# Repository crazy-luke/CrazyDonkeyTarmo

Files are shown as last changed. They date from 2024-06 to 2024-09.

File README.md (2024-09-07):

## [English README](./README_EN.md) 👈
----

# CrazyDonkeyTarmo

`CrazyDonkeyTarmo` 项目目标是保留高性能RC车乐趣的同时能开展学习自动驾驶技术。  
项目深度改造 Tarmo5 RC 车， 结合 DonkeyCar 自动驾驶项目。

## 视频介绍
* 《造车篇》： https://www.bilibili.com/video/BV1qM4m1U7vm
* 《自动驾驶篇》: https://www.bilibili.com/video/BV12aHZeXEUs

---
## 车辆制作 (Hardwear_Car)
* [CDT_Assemble.pdf](./Hardwear_Car/CDT_Assemble.pdf) ： 组装说明书
* STL： 3D 打印文件 （打印参数见 `stl/README.md` )
* [Parts.md](./Hardwear_Car/Parts.md): 视频中使用的部分零件

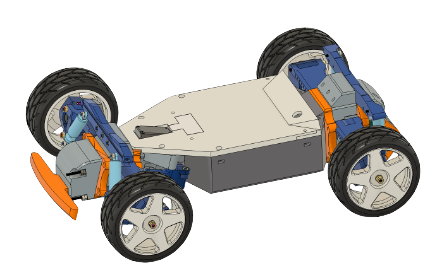
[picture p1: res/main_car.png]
main_car
 

## PCB电路 （Optinal)
* PCB_CrazyDonkeyTarmoBoard：超级电源板 
* PCB_CrazyPowerBoard： 探路者控制板 
    * BOM.csv: 采购元件清单
    * ibom.html：元件摆放(细节见PNG图片)
    * Gerber：PCB生产
    * Schematic：原理图
* 电路连接: [Wiring Diagram.jpg](./Hardwear_Car/wiring_diagram.jpg)

---
## 自动驾驶篇 (Softwear_SelfDrive)
* [星辰探路者自动驾驶系统手册](./Softwear_SelfDrive/README.md)
* [扩展篇-物件识别](./Softwear_SelfDrive/crazydonekytarmo_od.md) （Optinal)
* myconfig: 探路者配置参考文件

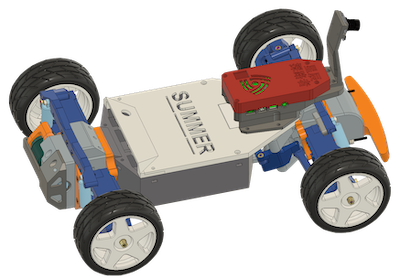
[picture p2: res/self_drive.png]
self_drive


## Reference
* [tarmo5](https://www.reddit.com/r/EngineeringNS/comments/zvellk/tarmo5/)
* [donkeycar](https://www.donkeycar.com/)

## License

<br />This work is licensed under a <a rel="license" href="http://creativecommons.org/licenses/by-nc-nd/4.0/">Creative Commons Attribution-NonCommercial-NoDerivatives 4.0 International License</a>.

Copyright © 2024, 疯狂豆®

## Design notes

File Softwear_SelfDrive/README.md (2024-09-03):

# 星辰探路者自动驾驶系统手册

本文描述基于 **Donkeycar** 搭建 **星辰探路者** 自动驾驶搭建全过程

## Hardware 
  * CrazyDonkeyTarmo 车
  * 树莓派
    * [Raspberry Pi](https://docs.donkeycar.com/guide/robot_sbc/setup_raspberry_pi/): 4B 4GB
    * [Camera](https://docs.donkeycar.com/parts/cameras/): 160 degree wide angle
    * microSD: 128G A2 U3 
      
------
##  一、安装系统
### Raspberry Pi

DonkeycarDoc:[Get Your Raspberry Pi Working](https://docs.donkeycar.com/guide/robot_sbc/setup_raspberry_pi/)

1. **安装树莓派 OS**
  * 操作： SD卡插入电脑
  * 安装工具: [Raspberry Pi Imager](https://www.raspberrypi.com/software/)
    * Choose
      * Choose divice: `raspberry pi 4`
      * Choose OS: `Raspberry Pi OS Lite 64-bit Bookworm`
      * Choose Storage: `SD`
    * Edit Settings
      * hostname: `crazydonkeytarmo-1`
      * username: `luke`, password: `123456`
      * SSID,  Password, Country
      * Enable SSH
  * 操作：SD插入树莓派，树莓派和电脑处于同一个网络，通电

  * 修改莓派修改配置
    
      ```
      # 电脑通过 SSH 连接树莓派
      # ssh username@ip
      # ssh username@hostname.local

      ssh luke@crazydonkeytarmo-1.local 

      # 进入配置
      sudo raspi-config
      ```
      配置界面依次选择：Advanced Options -> Expand Filesystem -> Finish -> reboot

2. **升级环境**

  * 升级软件包
    ```
    # Update and Upgrade
    sudo apt-get update --allow-releaseinfo-change
    sudo apt-get upgrade
    ```

  * 设置 Python 虚拟环境
    ```
    #创建一个名为env的虚拟环境，命令执行完毕后会出现一个env文件夹
    python3 -m venv env --system-site-packages

    #每次开机都会自动进入env的虚拟环境
    echo "source ~/env/bin/activate" >> ~/.bashrc
    source ~/.bashrc
    ```

  * 提前安装后续可能遇到错误的库（optinal)
    ```
    # libcap：捕获 过滤 分析 存储网络数据包
    sudo apt install libcap-dev

    # psutil：获取系统的信息， h5py：读写HDF5文件格式
    sudo apt-get install gcc python3-dev
    pip install psutil
    pip install h5py --only-binary h5py

    # python3-libcamera: 摄像头
    sudo apt install -y python3-libcamera
    
    # python3-kms++
    sudo apt install -y python3-kms++
    ```

3. **Donkeycar Code**

  * 下载源码
    ```
    # 安装git库
    sudo apt install git

    # 下载Git代码
    cd ~
    git clone https://github.com/autorope/donkeycar.git
    cd donkeycar
    
    # 切换版本
    git checkout 5.1.0

    # 编译安装 
    pip install -e .[pi]
    # zsh shell
    pip install -e .\[pi\]
    ```

  * 验证 tensorflow (optinal)
  ```
  python -c "import tensorflow; print(tensorflow.__version__)"
  ```

### 创建 CrazyDonkeyTarmo

1. [Create your car application 创建应用](https://docs.donkeycar.com/guide/create_application/)

    ```
    donkey createcar --path ~/crazydonkeytarmo

    cd ~/crazydonkeytarmo
    ```

2. 配置 [控制器](https://docs.donkeycar.com/parts/rc/)

  * 启用 pigpiod
    ```
    sudo systemctl enable pigpiod & sudo systemctl start pigpiod
    ```

  * 编辑 ~/crazydonkeytarmo/myconfig.py

    1. 从树莓派下载 myconfig.py 文件到电脑
    ```
    #电脑开一个新的终端
    #scp <username>@<ip>:<src_file> <des_file>

    scp luke@crazydonkeytarmo-1.local:/home/luke/crazydonkeytarmo/myconfig.py .
    ```

    2. 电脑打开 myconfig.py 文件并修改下面字段

    * 开启 pigpio
      ``` 
      CONTROLLER_TYPE = 'pigpio_rc'
      USE_JOYSTICK_AS_DEFAULT = True
      DRIVE_TRAIN_TYPE = "PWM_STEERING_THROTTLE"
      ```
    * 修改 PWM 输入信号（RC接收机 -> 树莓派）
      ```
      #PIGPIO RC control
      STEERING_RC_GPIO = 3              # CrazyDonkeyTarmoBus - s_in
      THROTTLE_RC_GPIO = 15             # CrazyDonkeyTarmoBus - t_in
      DATA_WIPER_RC_GPIO = 4            # CrazyDonkeyTarmoBus - ext
      PIGPIO_STEERING_MID = 1500         # Adjust this value if your car cannot run in a straight line
      PIGPIO_MAX_FORWARD = 2000          # Max throttle to go fowrward. The bigger the faster
      PIGPIO_STOPPED_PWM = 1500
      PIGPIO_MAX_REVERSE = 1000          # Max throttle to go reverse. The smaller the faster
      PIGPIO_SHOW_STEERING_VALUE = False
      PIGPIO_INVERT = False
      PIGPIO_JITTER = 0.025   # threshold below which no signal is reported
      ```
    * 打开 PWM 输出配置 （树莓派 -> 方向舵机和动力电机）
      ```
      # 打开PWM_STEERING_THROTTLE字段，修改PIN
      PWM_STEERING_THROTTLE = {
          "PWM_STEERING_PIN": "PIGPIO.BCM.2",   # CrazyDonkeyTarmoBus - s-out
          "PWM_THROTTLE_PIN": "PIGPIO.BCM.14",  # CrazyDonkeyTarmoBus - t-out
          .....
      }
      ```
    
    * 其他配置  Optinal
      ```
      # 修改摄像头
      CAMERA_TYPE = "PICAM"
      IMAGE_W = 320
      IMAGE_H = 240

      # 关闭自动录制
      AUTO_RECORD_ON_THROTTLE = False
      ```

    * 修改后的 myconfig.py 文件上传到树莓派
    ```
    #电脑 -> 树莓派
    #scp <src_file> <username>@<ip>:<des_file>

    scp myconfig.py luke@crazydonkeytarmo-1.local:/home/luke/crazydonkeytarmo/
    ```    

4. 测试
  注意：**关闭ESC电调开关**

  * 启动 crazydonkeytarmo应用
    ```
    #终端连接树莓派
    ssh luke@crazydonkeytarmo-1.local 

    #启动
    cd ~/crazydonkeytarmo
    python manage.py drive
    ```
  * 电脑浏览器访问
    http://ip:8887/drive
   
    如 http://crazydonkeytarmo-1.local:8887/drive

  * 关闭crazydonkeytarmo应用
  终端 `ctrl+c`

### 校准 

1. 官方[驴车参数](https://docs.donkeycar.com/parts/rc_hat/#controlling-esc-and-steering-servo-with-rc-hat)

2. CrazyDonkeyTarmo 参考参数
```
# 注：RC 接收机58hz,官方默认参数60hz, 修改 SCALE 为1.03
PWM_STEERING_THROTTLE = {
    "PWM_STEERING_PIN": "PIGPIO.BCM.2",   # PWM output pin for steering servo
    "PWM_STEERING_SCALE": 1.03,             # used to compensate for PWM frequency differents from 60hz; NOT for adjusting steering range
    "PWM_STEERING_INVERTED": False,         # True if hardware requires an inverted PWM pulse
    "PWM_THROTTLE_PIN": "PIGPIO.BCM.14",   # PWM output pin for ESC
    "PWM_THROTTLE_SCALE": 1.0,              # used to compensate for PWM frequence differences from 60hz; NOT for increasing/limiting speed
    "PWM_THROTTLE_INVERTED": False,         # True if hardware requires an inverted PWM pulse
    "STEERING_LEFT_PWM": 200,               #pwm value for full left steering
    "STEERING_RIGHT_PWM":400,              #pwm value for full right steering
    "THROTTLE_FORWARD_PWM": 400,            #pwm value for max forward throttle
    "THROTTLE_STOPPED_PWM": 300,            #pwm value for no movement
    "THROTTLE_REVERSE_PWM": 200,            #pwm value for max reverse throttle
}
```

------
## 二、自动驾驶

### 收集训练数据
* 树莓派连接手机[网络(Bookworm)](https://www.raspberrypi.com/documentation/computers/configuration.html#configuring-networking)
  ```
  #终端连接树莓派
  ssh luke@crazydonkeytarmo-1.local 

  #查看网络
  sudo nmcli dev wifi list

  #连接网络 (例如 AiPhone)
  sudo nmcli --ask dev wifi connect AiPhone

  #查看网络连接优先级
  nmcli --fields autoconnect-priority,name connection

  #调整优先级（数字越大优先级越高）
  sudo nmcli connection modify AiPhone connection.autoconnect-priority 2
  ```
* 手机安装SSH应用 APP ： `Termius`

2. 采集训练数据

* SSH 连接树莓派
  ```
  ssh luke@crazydonkeytarmo-1.local 
  cd crazydonkeytarmo

  #清理历史数据(optinal)
  #rm -rf ./data/*

  #开始驾驶
  python manage.py drive
  ```
* 开始录制
浏览器访问 http://crazydonkeytarmo-1.local:8887/drive
User-> Start Reconrding
**Let's Go~~~~**

### 训练数据
1. 树莓派训练数据上传到电脑
```
## 树莓派crazydonkeytarmo 目录同步下载到电脑上（初次）
rsync -rv --progress --partial luke@crazydonkeytarmo-1.local:~/crazydonkeytarmo/  ./crazydonkeytarmo

## 树莓派 data目录同步下载到电脑上 crazydonkeytarmo 目录中
# cd crazydonkeytarmo 
# rsync -rv --progress --partial luke@crazydonkeytarmo-1.local:~/crazydonkeytarmo/data/  ./data
```

2. 电脑安装 donkeycar （初次)
```
git clone https://github.com/autorope/donkeycar.git
cd donkeycar
git checkout 5.1.0

#删除已经存在的环境
#conda activate base
#sudo conda env remove -n donkey

conda create -n donkey python=3.11
conda activate donkey
#确认当前已经处于 donkey
conda env list  

#安装
#pip install donkeycar\[pc\]
pip install -e .\[pc\]
```

3. [训练模型](https://docs.donkeycar.com/guide/deep_learning/train_autopilot/)
  
  * 启动donkey ui
    ```
    conda activate donkey
    sudo donkey ui
    ``` 
    * Load car directory:  选择 crazydonkeycar 目录
    * Load tube: 选择 crazydonkeycar 中的data目录（训练数据）
    * Delete: 删除不需要的数据区域(optinal)

  * 通过 [donkey ui](https://docs.donkeycar.com/utility/ui/) 训练
    `Trainer -> Train`
  * 通过命令行训练（optinal, 适合数据量较大)
    ```
    # 用 data 目录下的数据训练一个名为 cdt1 的模型
    donkey train --tub ./data  --model ./models/cdt1
    ```
  * [Train model using GPU for FREE on google golab](https://colab.research.google.com/drive/1CALMB7GioBEUcWNCuHQjrWCT4r01p6Qh)
4. 可能遇到的错误(optinal)
     
     ```
     ## v5.1.0  
     ## ValueError: Key image is not in available keys.
     ## fix: 设置 albumentations==1.4.6
     sudo pip uninstall -y albumentations && pip install albumentations==1.4.6
     ```

### 开始自动驾驶

1. 上传训练完成的 Model 到树莓派
   ```
   #上传模型到树莓派
   #进入电脑的 crazydonkeytarmo 目录执行
   rsync -rv --progress --partial ./models/ luke@crazydonkeytarmo-1.local:~/crazydonkeytarmo/models/
   ```
2. 自动驾驶
    ```
    # 连接 树莓派
    ssh luke@crazydonkeytarmo-1.local 
    cd ~/crazydonkeytarmo

    # 启动模型
    python manage.py drive --model ./models/cdt1.tflite --type tflite_linear
    ```

### 扩展篇
  
 [物件识别](./crazydonekytarmo_od.md)

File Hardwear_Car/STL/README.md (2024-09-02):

# CrazyDonkeyTarmo PRINTED PARTS
---
> Filament:  
> `ABS`: 20% lighter compared to PETG  (ABS 比 PETG重量轻20%)  
> `PETG`: More resistant to UV light compared to ABS  (PETG 比 ABS 更耐紫外线)

## Main Parts
| File | Num | filament  | fill | wall| supports|
| ---|:---:| ---:| ----:|----:|----:|
| TORQUE DAMPER Fit | 2 | TPU95 | 100% | 8 | No
| MOTO MOUNT Fit | 1 | TPU95 | 10% | 6 | No
| FRONT A PLATE FIT | 1 | TPU95 | 10% | 8 | No
| FRONT B PLATE | 1 | TPU95 | 10% | 8 | No
| REAR A PLATE FIT  | 1 | TPU95 | 10% | 8 | No
| REAR B PLATE | 1 | TPU95 | 10% | 8 | No
| Bumper | 1 | TPU95 | 10% | 4 | No
| CONTROL ARM FIT | 8 | ABS/PETG | 10% |9| YES
| FRONT BEARING HUB A05 Fit | 1 | ABS/PETG | 10% |8| No
| FRONT BEARING HUB A06 Fit | 1 | ABS/PETG | 10% |8| No
| FRONT SUS MOUNT Fit | 2 | ABS/PETG | 10% |8| YES
| FRONT AXLE Fit | 2 | PACF  | 10% |8| No
| MAIN GEAR HUB | 1 | PACF  | 10% |8| No
| REAR BEARING HUB  | 2 | ABS/PETG | 10% |8| No
| SHOCK MOUNT FRONT Fit|1 |PACF/PETG  | 10% | 12 or 8| NO
| SHOCK MOUNT REAR Fit  | 1 | PACF/PETG  | 10% |8| No
| STEERING BAR Fit DS3225  | 1 | ABS/PETG | 10% |8| NO
| STEERING ARM A07 FIT  | 1 | ABS/PETG  | 10% |8| YES
| STEERING ARM A08 FIT | 1 | ABS/PETG  | 10% |8| YES
| GEARBOX | 1| ABS/PETG | 10% |3| No
| END CHASSIS B05 | 1| ABS/PETG | 10% |3| No
| END CHASSIS B06 | 1| ABS/PETG | 10% |3| No
| END CHASSIS B04 Fit| 1| ABS/PETG | 10% |3| YES
| GEARBOX LID | 1| ABS/PETG | 10% |3| YES
| CHASSIS Ext | 1 | ABS/PETG | 10% |3| YES
| CHASSIS Cover body | 1 | ABS/PETG | 10% |3| NO
| CHASSIS Cover rear | 1 | ABS/PETG | 10% |3| NO
| CHASSIS Cover window  | 1 | ABS/PETG | 10% |3| NO
| MAIN GEAR herringbone  | 1 | PA/ABS  |  10% |8| NO
| PINION GEAR herringbone  | 1 | PA/ABS  |  10% |8| NO
| STEERING Link Fit  | 2 | PA/PACF | 20% |8| NO
| CV CAGE Fit | 4 | PACF | 10% |8| NO
| CV INNER RACE | 4 | PACF | 10% |8| No
| CV WHEEL HOUSING Fit  | 2 | PACF | 10% |8| No
| FRONT WHEEL SPACER Fit | 4 | PACF | 10% |8| No
| CV GEAR HOUSING Fit  | 2 | PACF | 10% |8| No

## Extension
| File | Num | filament  | fill | wall| supports|
| ---|:---:| ---:| ----:|----:|----:|
| SHOCK MOUNT FRONT LIGHT|1 |PACF/PETG/ABS| 10% | 12 or 8| NO
| LIGHT Wire Cover H | 1 | - | 10% | 3 | NO
| Cover_rear_Light_L  | 1 | - | 10% | 3 | NO
| Cover_rear_Light_LH  | 1 | - | 10% | 3 | NO
| CrazyPowerBoard_Base  | 1 | - | 10% | 3 | NO

## Self Drive Parts

| File | Num | filament  | fill | wall| supports|
| ---|:---:| ---:| ----:|----:|----:|
| FSD_Cam | 1 | - | 10% | 3 | NO
| FSD_Shell_cover | 1 | - | 10% | 3 | NO
| FSD_Shell_main | 1 | - | 10% | 3 | NO
| FSD_Bottom | 1 | - | 10% | 3 | NO

----
## My Print settings 
* PACF
```
Printing Temperature : 255
Print Speed : 80～100
Build Plate Temperature : 70
Fan Speed : OFF
```

* PA12
```
Printing Temperature : 270
Build Plate Temperature : 80
Print Speed : 100
Fan Speed 20%
```

* TPU95
```
Printing Temperature : 235
Build Plate Temperature : 50
Print Speed : 55
Fan Speed : 100%
```

* PETG
```
Printing Temperature : 240
Build Plate Temperature : 55
Print Speed : 170
Fan Speed : 50%
```

* ABS
```
Printing Temperature : 240
Build Plate Temperature : 95
Print Speed : 160
Fan Speed : 30%
```

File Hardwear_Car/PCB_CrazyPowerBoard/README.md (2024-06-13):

# CrazyDonkeyTarmo

Todo: Currently being organized, please be patient.
项目资料还在更新中，目前已经开放 RC 车制作部分。

CrazyDonkeyTarmo 项目目标是保留高性能RC车乐趣的同时能开展学习自动驾驶技术。
项目深度改造 Tarmo5 RC 车， 结合 DonkeyCar 自动驾驶项目。

----
## 车辆硬件制作
* CDT_Assemble.pdf ： 组装说明 (P1-车辆)
* STL： 3D 打印文件
main_car

## PCB电路 （Optinal)
* PCB_CrazyPowerBoard： 探路者控制板 
* PCB_CrazyDonkeyTarmoBoard：超级电源板 

## 自动驾驶篇 (Todo)
Todo

## Reference
* [tarmo5](https://www.reddit.com/r/EngineeringNS/comments/zvellk/tarmo5/)
* [donkeycar](https://www.donkeycar.com/)

## License

<br />This work is licensed under a <a rel="license" href="http://creativecommons.org/licenses/by-nc-nd/4.0/">Creative Commons Attribution-NonCommercial-NoDerivatives 4.0 International License</a>.

Copyright © 2024, 疯狂豆®

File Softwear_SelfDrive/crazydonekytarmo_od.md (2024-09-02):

# 星辰探路者自动驾驶系统手册（扩展篇）

本文描述基于 **Mediapipe** 识别目标增强探路者自动驾驶能力。
内容包括：  
1. 使用预训练模型 识别 `STOP` 标志，车辆执行动作： **停止 -> 等待 -> 前进**
2. 使用预训练模型 识别特定物件， 车辆执行动作：**绕过障碍物**
3. 使用 MediaPipe Maker 迁移学习训练自定义模型 

## Object Detection 测试

### 电脑上测试
* [MediaPipe studio](https://mediapipe-studio.webapps.google.com/home)
* [Labelmap](https://storage.googleapis.com/mediapipe-tasks/object_detector/labelmap.txt)
* [Models](https://ai.google.dev/edge/mediapipe/solutions/vision/object_detector#configurations_options)

### 树莓派上运行 Demo

1. Google 官方样例

  [MediaPipe for Raspberry Pi](https://github.com/google-ai-edge/mediapipe-samples/tree/main/examples/object_detection/raspberry_pi)

```
# SSH 连接树莓派
ssh luke@crazydonkeytarmo-1.local 

# 下载代码
cd ~
git clone https://github.com/google-ai-edge/mediapipe-samples.git

# 设置环境，下载模型
cd mediapipe-samples/examples/object_detection/raspberry_pi
sh setup.sh

# 安装缺少 OpenCV 依赖的 OpenGL 库 (Optinal)
sudo apt install -y libgl1-mesa-glx

# 运行
python3 detect.py   --model efficientdet.tflite

## 摄像头驱动问题，报错和解决参考
# ERROR: Unable to read from webcam. Please verify your webcam settings.
>> https://github.com/google-ai-edge/mediapipe-samples/issues/383

```

2. 星辰探路者 测试代码
   
```
# 上传 mediapipe_cdt
rsync -rv --progress --partial ./mediapipe_cdt/ luke@crazydonkeytarmo-1.local:~/mediapipe_cdt/

# SSH 连接树莓派
ssh luke@crazydonkeytarmo-1.local 
cd mediapipe_cdt

# 下载模型文件 efficientdet_lite0.tflite
wget -q -O efficientdet_lite0.tflite -q https://storage.googleapis.com/mediapipe-models/object_detector/efficientdet_lite0/int8/1/efficientdet_lite0.tflite

# 运行 
# Headless (Text Only)
python3 detect_cdt_text.py   --model efficientdet_lite0.tflite --maxResults 2 --scoreThreshold 0.51 --frameWidth 320 --frameHeight 240

```
```
#fix issue: module 'cv2' has no attribute 'flip'
pip install opencv-python

Looking in indexes: https://pypi.org/simple, https://www.piwheels.org/simple
Collecting opencv-python
  Using cached opencv_python-4.10.0.84-cp37-abi3-manylinux_2_17_aarch64.manylinux2014_aarch64.whl.metadata (20 kB)
Requirement already satisfied: numpy>=1.21.2 in /home/luke/env/lib/python3.11/site-packages (from opencv-python) (1.26.4)
Using cached opencv_python-4.10.0.84-cp37-abi3-manylinux_2_17_aarch64.manylinux2014_aarch64.whl (41.7 MB)
Installing collected packages: opencv-python
Successfully installed opencv-python-4.10.0.84
```

## 使用预训练模型

👉 [MR to donkeycar](https://github.com/autorope/donkeycar/pull/1197)

工程改动说明
```
- donkeycar/donkeycar/parts/object_detector/
├── mediapipe_object_detetor.py   ## mediapipe object detection
├── detector_manager.py           ## 识别模块总调度
├── action_stop_and_go.py         ## StopAndGo  停止车辆 -> 等待 -> 前进
├── action_pass_object.py         ## PassObject 绕过障碍物

- donkeycar/donkeycar/templates/
├── complete.py         ## 加载 detector_manager 模块
├── cfg_complete.py     ## 增加 object detection 开关配置

- donkeycar/
├── setup.cfg           ## 增加 mediapipe 依赖

```

创建新应用
```
# SSH 连接树莓派
ssh luke@crazydonkeytarmo-1.local 
cd donkeycar

# 安装依赖 
pip install mediapipe

# 编译(optinal)
pip install -e .[pi]
# pip install -e .\[pi\]

# 创建新应用 crazydonkeytarmo_od
donkey createcar --path ~/crazydonkeytarmo_od
cd ~/crazydonkeytarmo_od

# 下载模型文件物件识别模型文件
# https://storage.googleapis.com/mediapipe-models/object_detector/efficientdet_lite0/int8/1/efficientdet_lite0.tflite
# 上传自定义物件识别模型
# scp android_toy_model.tflite luke@crazydonkeytarmo-1.local:/home/luke/crazydonkeytarmo/

# 上传文件到树莓派：修改后的配置, 自动驾驶驾驶模型，物件识别模型
rsync -rv --progress --partial ./crazydonkeytarmo_od/ luke@crazydonkeytarmo-1.local:~/crazydonkeytarmo_od/
```

# 运行自动驾驶

* 测试识别指定标签
* `STOP` 标志动作
* 绕过障碍物

```
cd crazydonkeytarmo_od

# 1. 配置 myconfig.py： OBJECT_DETECTOR 

# 2. 运行
python manage.py drive --model ./models/cdt1.tflite --type tflite_linear

# 3. 浏览器访问 http://crazydonkeytarmo-1.local:8887/drive
```

## Transefer 训练自己的模型

[MediaPipe model maker](https://ai.google.dev/edge/mediapipe/solutions/model_maker)

[Object detection model customization](https://ai.google.dev/edge/mediapipe/solutions/customization/object_detector)

## Ref

* [mediapipe-samples: object detection on raspberry](https://github.com/google-ai-edge/mediapipe-samples/tree/main/examples/object_detection/raspberry_pi)

* [MediaPipe maker exaple: Object_Detection_for_3_dogs](https://colab.research.google.com/github/googlesamples/mediapipe/blob/main/tutorials/object_detection/Object_Detection_for_3_dogs.ipynb)

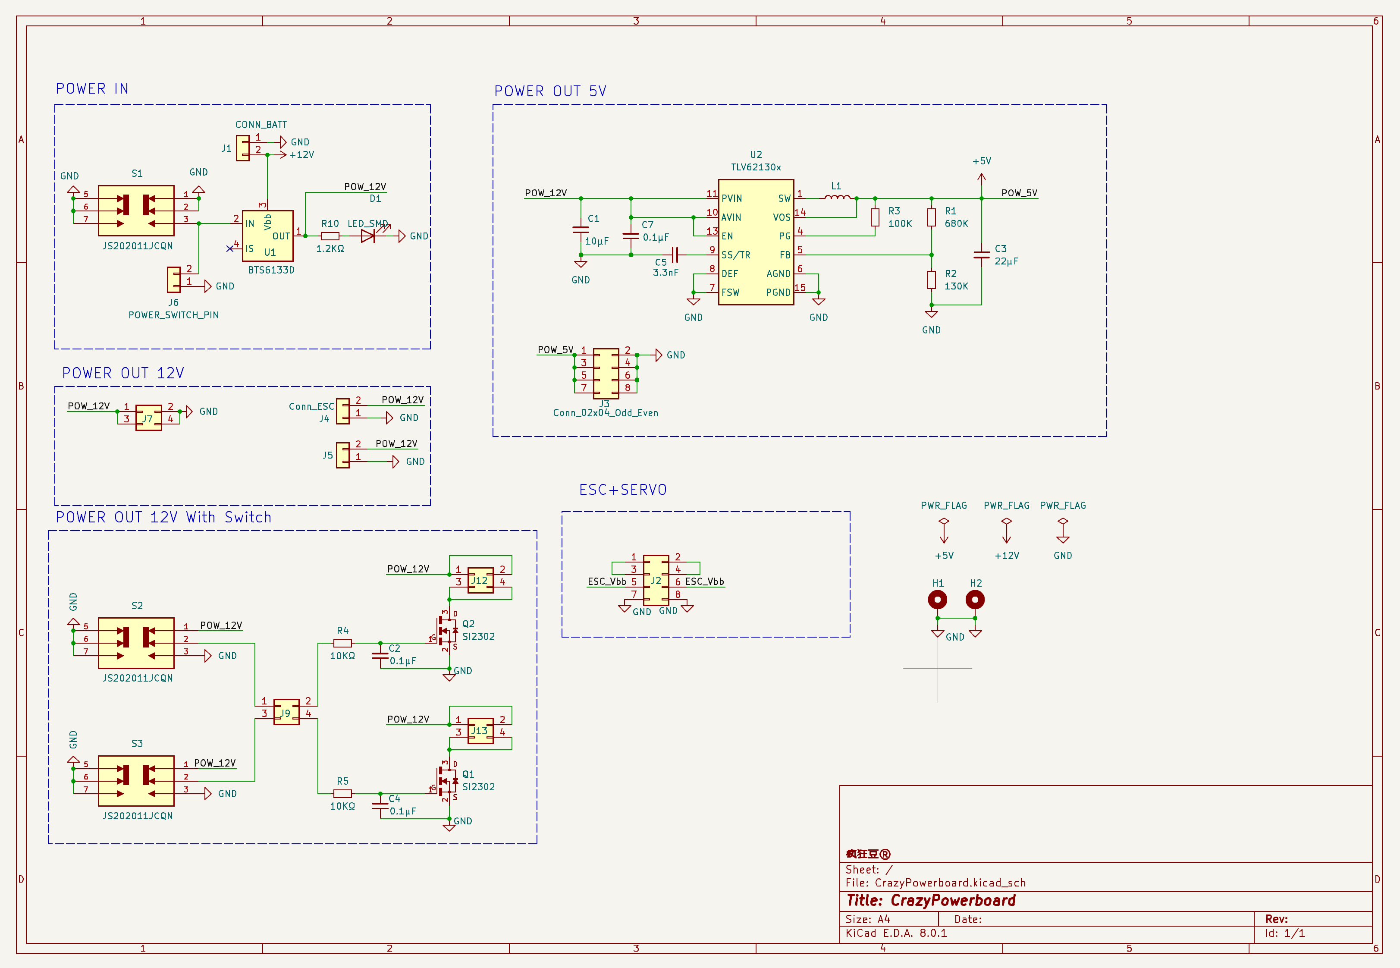
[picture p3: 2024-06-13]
Hardwear_Car/PCB_CrazyPowerBoard/Schematic.png

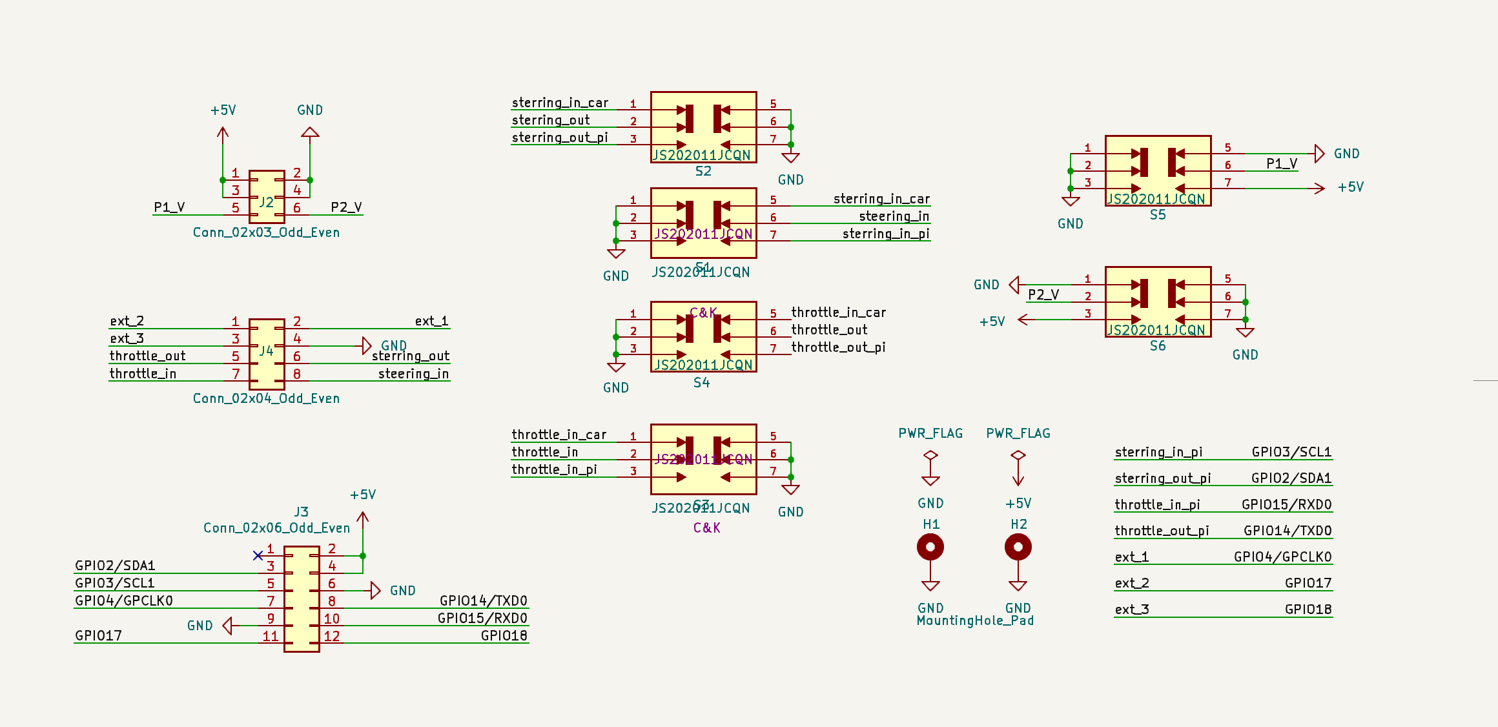
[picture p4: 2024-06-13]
Hardwear_Car/PCB_CrazyDonkeyTarmoBoard/Schematic.png

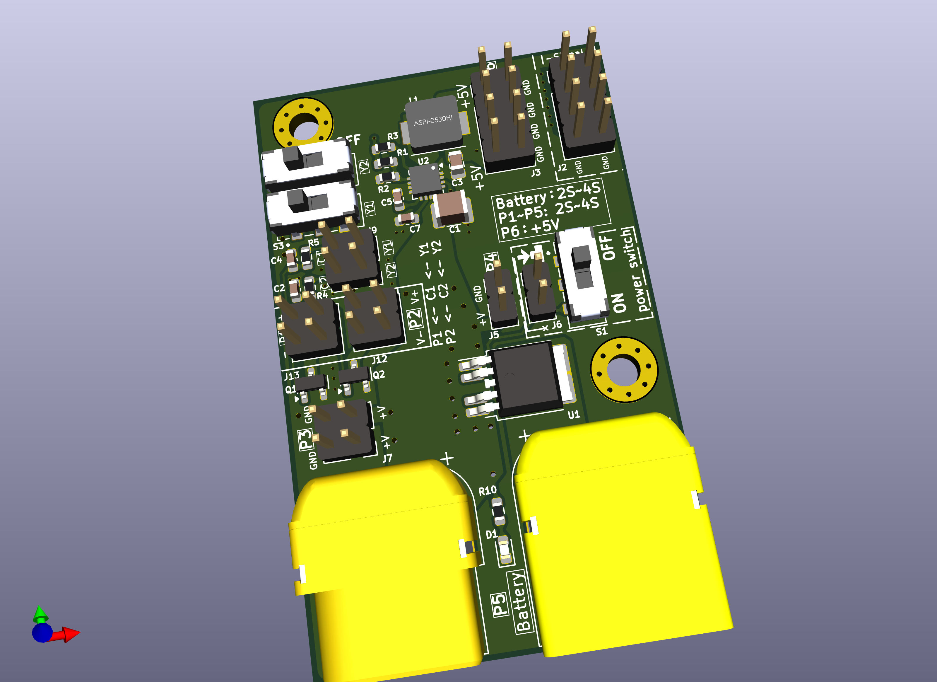
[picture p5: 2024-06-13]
Hardwear_Car/PCB_CrazyPowerBoard/CrazyPowerboard_1.png

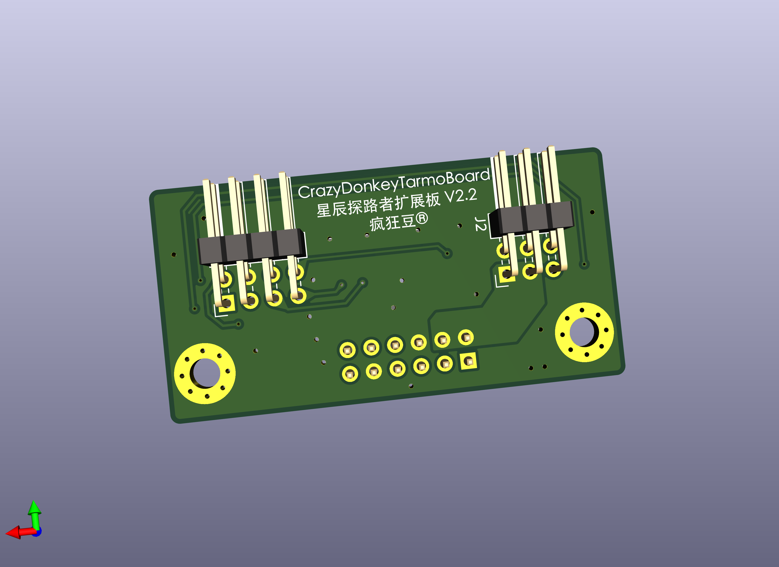
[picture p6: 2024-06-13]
Hardwear_Car/PCB_CrazyDonkeyTarmoBoard/CrazyDonkeyTarmoBoard_2.png

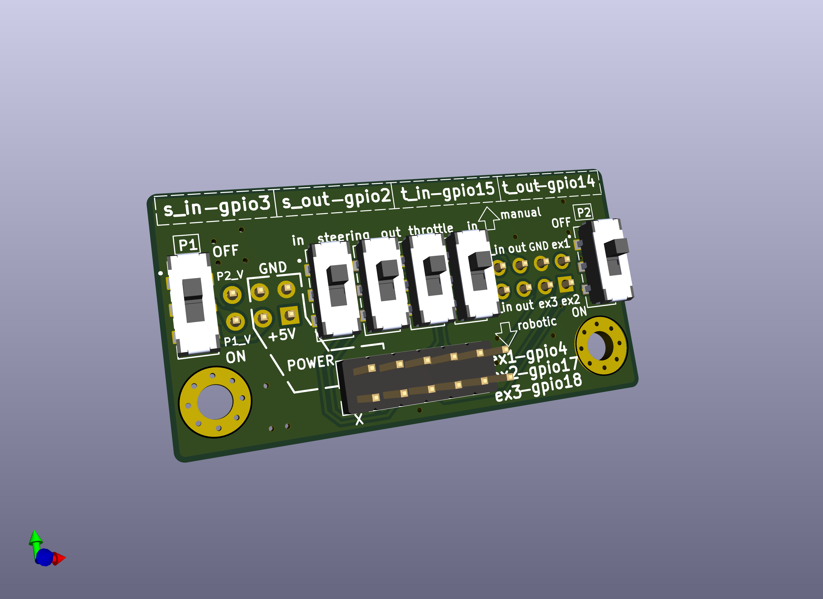
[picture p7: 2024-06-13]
Hardwear_Car/PCB_CrazyDonkeyTarmoBoard/CrazyDonkeyTarmoBoard_1.png

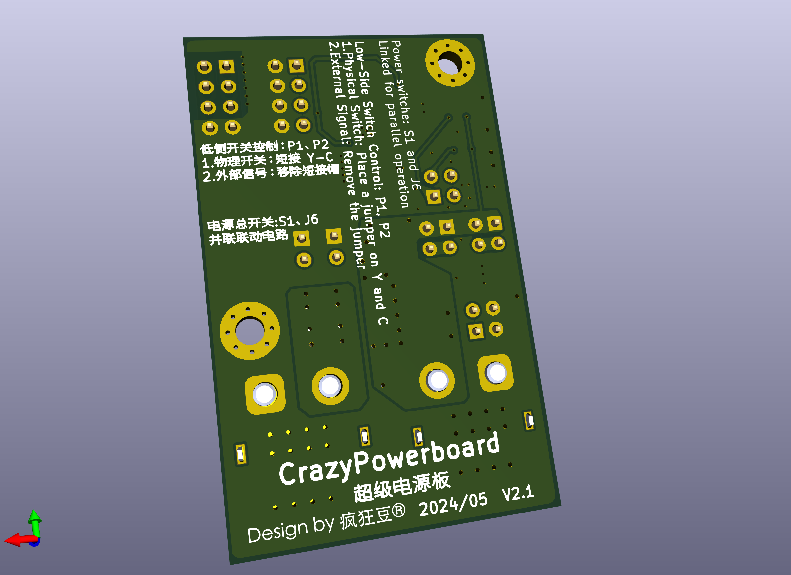
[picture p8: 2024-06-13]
Hardwear_Car/PCB_CrazyPowerBoard/CrazyPowerboard_2.png

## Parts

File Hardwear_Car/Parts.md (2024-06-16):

#  BOM
These are the parts as shown in the video.
视频中部分同款零件

* **Motor**
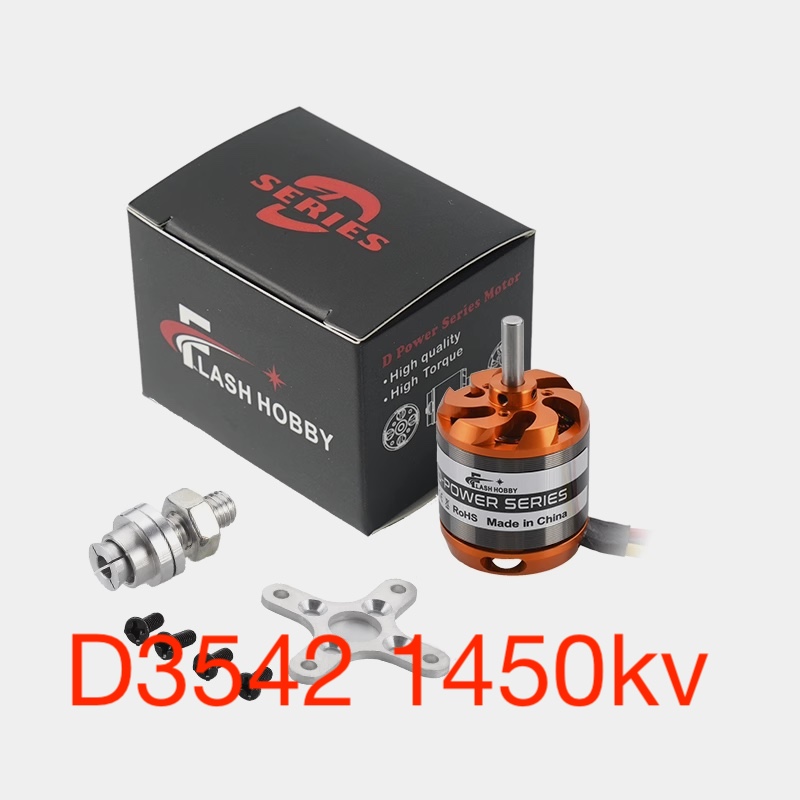
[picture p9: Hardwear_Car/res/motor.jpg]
motor


* **Servo**
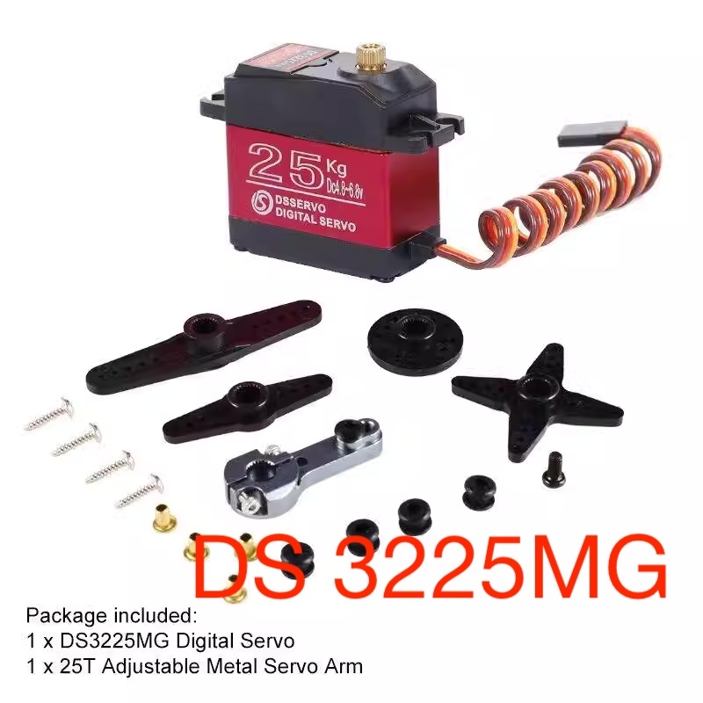
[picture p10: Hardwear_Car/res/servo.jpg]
servo


* **Tire**
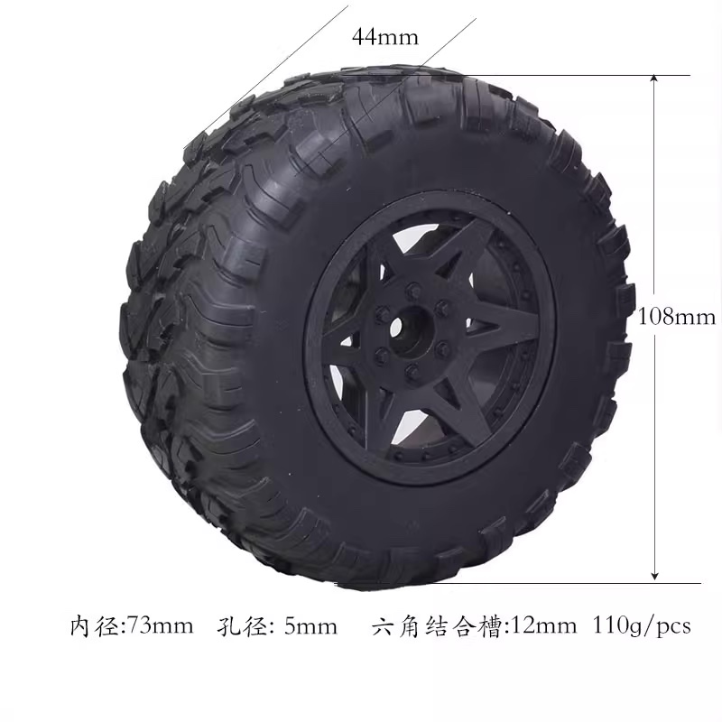
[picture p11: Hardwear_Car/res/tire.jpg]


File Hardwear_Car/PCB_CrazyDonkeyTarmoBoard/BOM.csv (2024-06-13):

Reference | Value | Datasheet | Footprint | Qty | Manufacturer | PartNumber
J2 | Conn_02x03_Odd_Even | ~ | Connector_PinHeader_2.54mm:PinHeader_2x03_P2.54mm_Horizontal | 1
J3 | Conn_02x06_Odd_Even | ~ | Connector_PinHeader_2.54mm:PinHeader_2x06_P2.54mm_Vertical | 1
J4 | Conn_02x04_Odd_Even | ~ | Connector_PinHeader_2.54mm:PinHeader_2x04_P2.54mm_Horizontal | 1
S1,S2,S3,S4,S5,S6 | JS202011JCQN | https://www.ckswitches.com/media/1422/js.pdf | CrazyDonkeyTarmoBoard:SW_JS202011JCQN | 6 | C&K | JS202011JCQN

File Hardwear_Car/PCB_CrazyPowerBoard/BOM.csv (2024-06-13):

Reference | Value | Footprint | Qty | Manufacturer | PartNumber | Description
C1 | 10µF | Capacitor_SMD:C_1210_3225Metric | 1 | SAMSUNG | CL32B106KAJNNNE | Capacitor 10 µF, 25 V, Ceramic, 1210
C2,C4,C7 | 0.1µF | Capacitor_SMD:C_0603_1608Metric | 3 | SAMSUNG | CL10B104KA8NNNC | Capacito 0.1 µF, 25V, Ceramic, 0603
C3 | 22µF | Capacitor_SMD:C_0805_2012Metric | 1 | YAGEO | CC0805KKX5R5BB226 | Capacitor 22 µF, Ceramic, 0805
C5 | 3.3nF | Capacitor_SMD:C_0603_1608Metric | 1 | YAGEO | CC0603JRX7R8BB332 | Capacitor 3300 pF, 25 V, Ceramic, 0603
D1 | LED_SMD | LED_SMD:LED_0603_1608Metric | 1 | Lite-On | LTST-C190GKT | Light emitting diode
H1,H2 | MH | MountingHole:MountingHole_3.2mm_M3_Pad_Via | 2 |  |  | Mounting Hole with connection
J1 | CONN_BATT | CrazyPowerboard:AMASS_XT60PW-M_1x02_P7.20mm_Horizontal | 1 | AMASS | XT60PW-M
J2,J3 | Conn_02x04_Odd_Even | Connector_PinHeader_2.54mm:PinHeader_2x04_P2.54mm_Vertical | 2 |  |  | PinHeader 2.54mm 2x04
J4 | Conn_ESC | CrazyPowerboard:AMASS_XT60PW-F_1x02_P7.20mm_Horizontal | 1 | AMASS | XT60PW-F
J5 | Conn_01x02 | Connector_PinHeader_2.54mm:PinHeader_1x02_P2.54mm_Vertical | 1 |  |  | PinHeader 2.54mm 2x01
J6 | POWER_SWITCH_PIN | Connector_PinHeader_2.54mm:PinHeader_1x02_P2.54mm_Vertical | 1 |  |  | PinHeader 2.54mm 2x01
J7,J9,J12,J13 | Conn_02x02_Odd_Even | Connector_PinHeader_2.54mm:PinHeader_2x02_P2.54mm_Vertical | 4 |  |  | PinHeader 2.54mm 2x02
L1 | ASPI-0530HI-2R2M-T2 | CrazyPowerboard:IND_ASPI-0530HI-2R2M-T2 | 1 | Abracon | ASPI-0530HI-2R2M-T2 | Inductor 2.2 µH
Q1,Q2 | SI2302 | Package_TO_SOT_SMD:SOT-23 | 2 | Vishay Siliconix |  | N-Channel 20 V 2.6A (Ta) 710mW (Ta) Surface Mount SOT-23-3 (TO-236)
R1 | 680K | Resistor_SMD:R_0603_1608Metric | 1 | YAGEO | RC0603FR-07680KL | Resistor, 100 kΩ, Chip, 0603, 1/16W, 1%
R2 | 130K | Resistor_SMD:R_0603_1608Metric | 1 | YAGEO | RC0603FR-07130KL | Resistor, 100 kΩ, Chip, 0603, 1/16W, 1%
R3 | 100K | Resistor_SMD:R_0603_1608Metric | 1 | YAGEO | RC0603FR-07100KL | Resistor, 100 kΩ, Chip, 0603, 1/16W, 1%
R4,R5 | 10KΩ | Resistor_SMD:R_0603_1608Metric | 2 | YAGEO | RC0603FR-071K2L
R10 | 1.2KΩ | Resistor_SMD:R_0603_1608Metric | 1 | YAGEO | RC0603FR-071K2L
S1,S2,S3 | JS202011JCQN | CrazyPowerboard:SW_JS202011JCQN | 3 | C&K | JS202011JCQN
U1 | BTS6133D | Package_TO_SOT_SMD:TO-252-4 | 1 | Infineon | BTS6133DAUMA1
U2 | TLV62130x | Package_DFN_QFN:VQFN-16-1EP_3x3mm_P0.5mm_EP1.68x1.68mm | 1 | Texas Instruments | TLV62130ARGTR | 3-V to 17-V 3-A Step-Down Converter, 2.5Mhz, VQFN-16

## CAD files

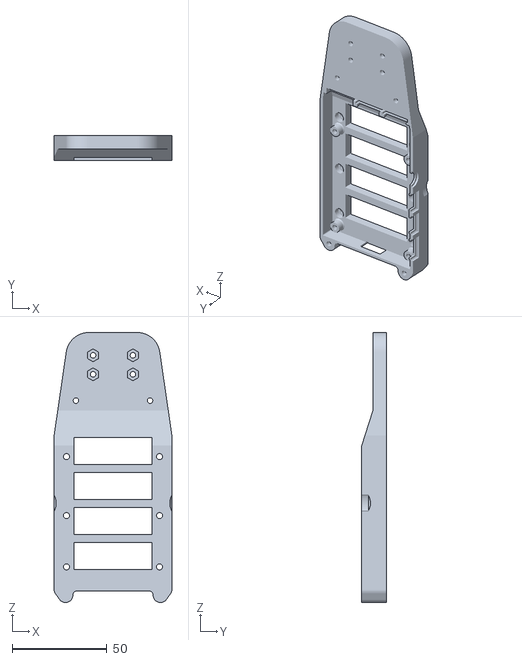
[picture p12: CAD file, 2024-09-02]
Hardwear_Car/STL/SelfDrive/FSD_Shell_main.stl
62.0 x 13.0 x 142.1

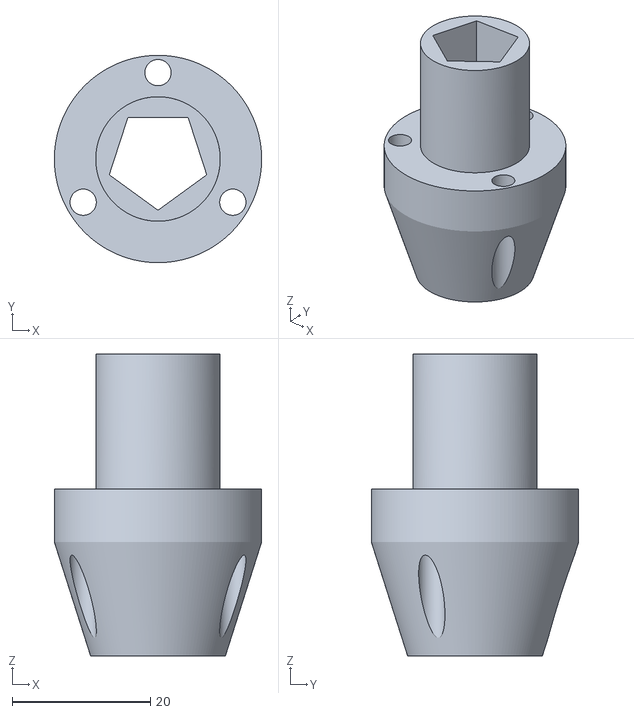
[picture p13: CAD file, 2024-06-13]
Hardwear_Car/STL/MainPart/MAIN GEAR HUB.stl
30.0 x 30.0 x 43.7

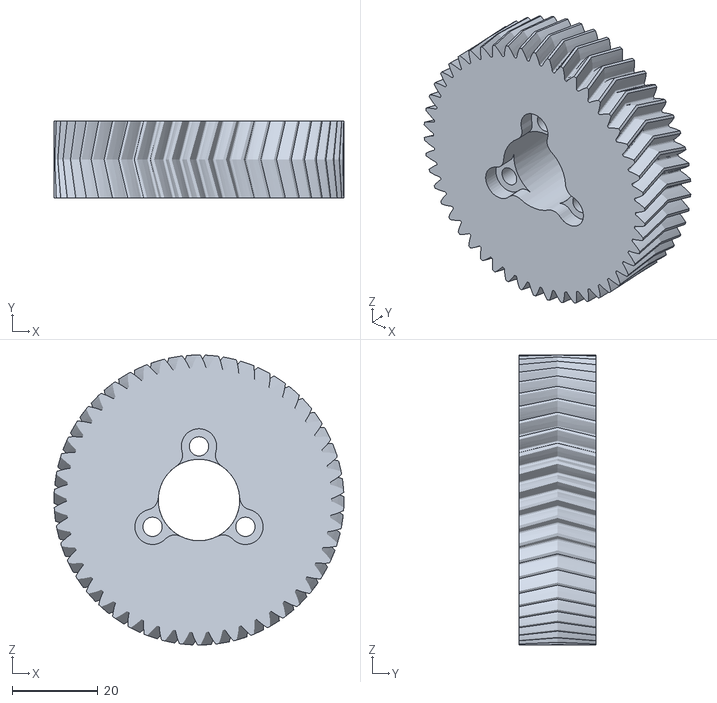
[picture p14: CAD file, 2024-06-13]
Hardwear_Car/STL/MainPart/MAIN GEAR herringbone.stl
67.6 x 18.0 x 67.6

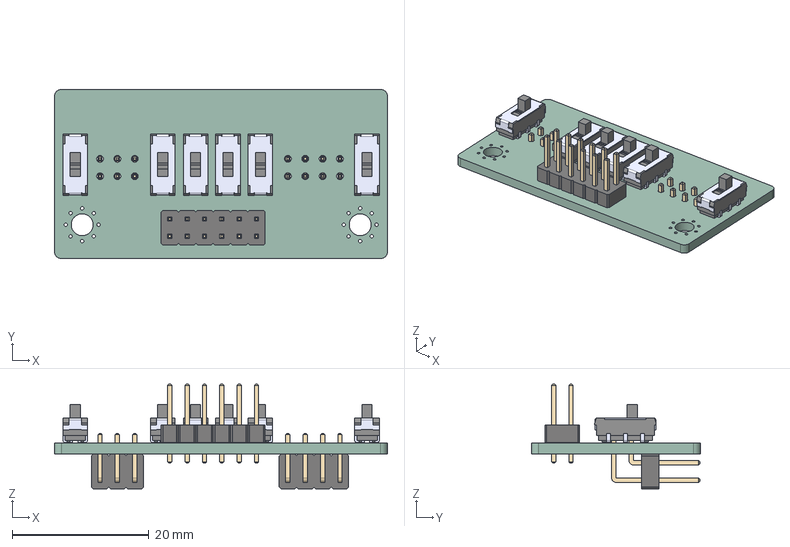
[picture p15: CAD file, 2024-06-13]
Hardwear_Car/PCB_CrazyDonkeyTarmoBoard/CrazyDonkeyTarmoBoard.step
48.8 x 24.8 x 15.3 mm
JS202011JCQN x 6
PinHeader_2x06_P254mm_Vertical
PinHeader_2x04_P254mm_Horizontal
PinHeader_2x03_P254mm_Horizontal
CrazyDonkeyTarmoBoard_PCB

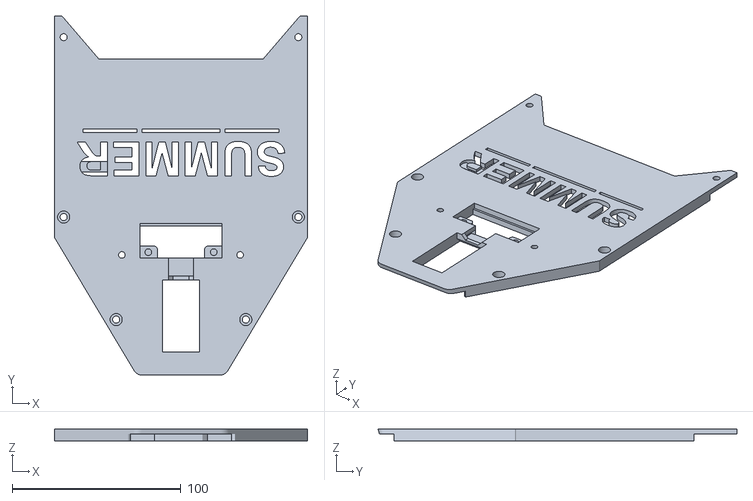
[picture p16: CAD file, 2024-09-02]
Hardwear_Car/STL/Extension/CHASSIS_Cover_summer.stl
150.0 x 212.6 x 7.00

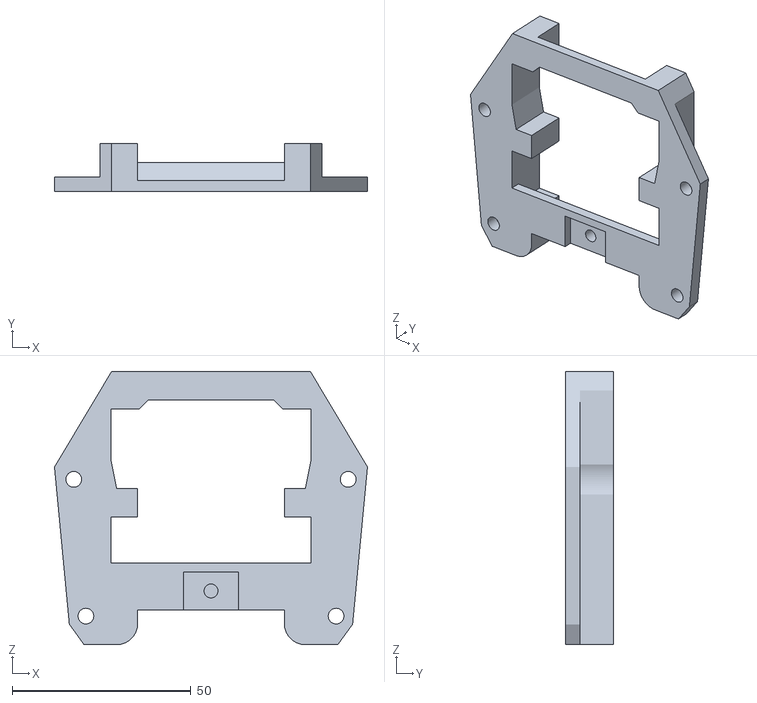
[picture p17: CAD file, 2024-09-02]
Hardwear_Car/STL/SelfDrive/FSD_Bottom.stl
87.6 x 13.4 x 76.5

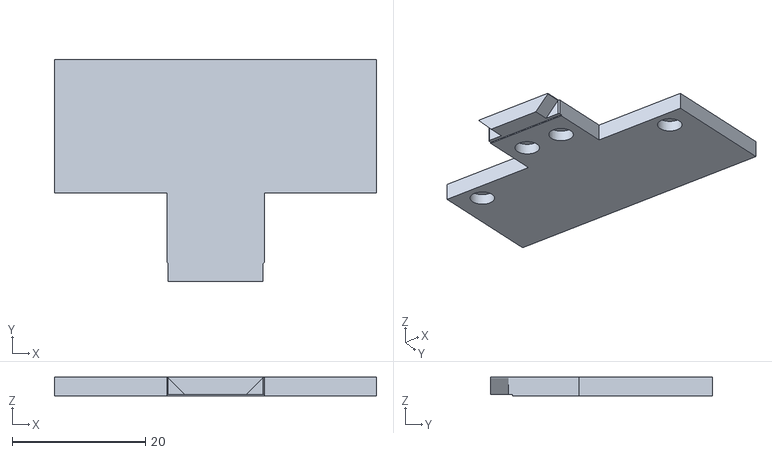
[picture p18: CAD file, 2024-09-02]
Hardwear_Car/STL/Extension/CHASSIS_Cover_window.stl
48.2 x 33.3 x 2.80

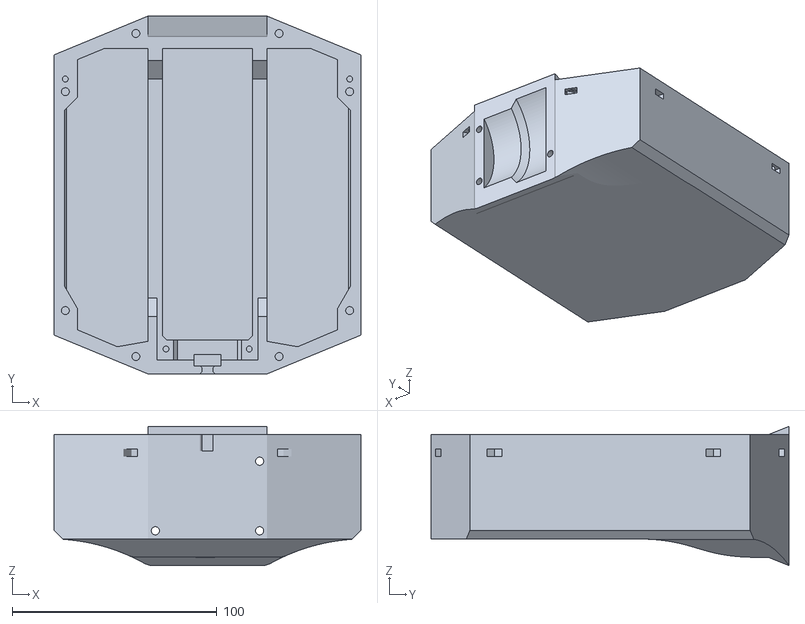
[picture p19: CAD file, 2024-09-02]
Hardwear_Car/STL/MainPart/CHASSIS Ext.stl
150.0 x 175.0 x 68.0

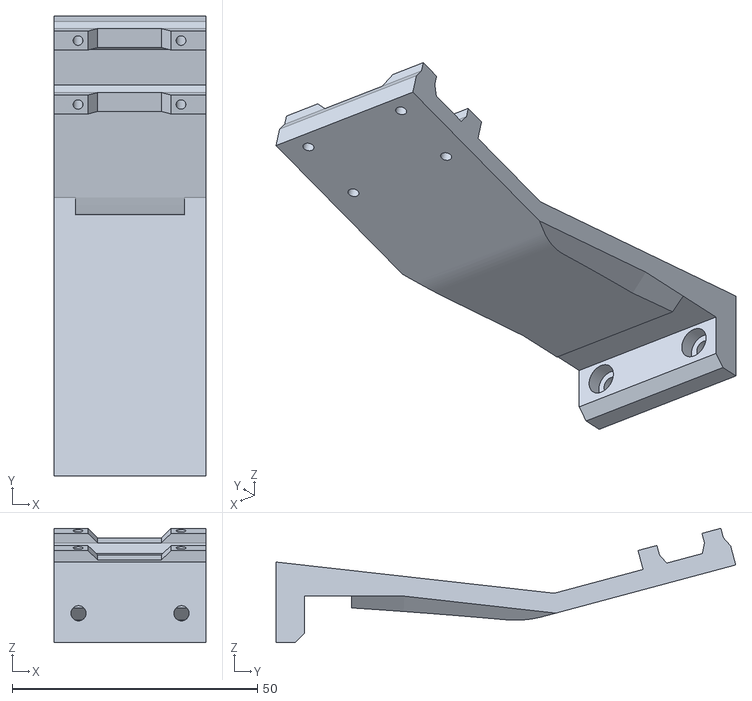
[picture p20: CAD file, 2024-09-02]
Hardwear_Car/STL/SelfDrive/FSD_Cam.stl
31.0 x 93.7 x 23.3

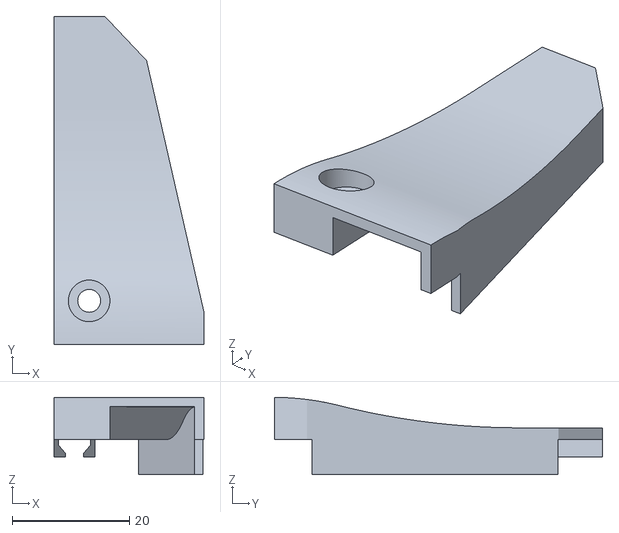
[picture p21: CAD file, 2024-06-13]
Hardwear_Car/STL/Extension/Cover_rear_Light_L.stl
25.6 x 56.0 x 13.2

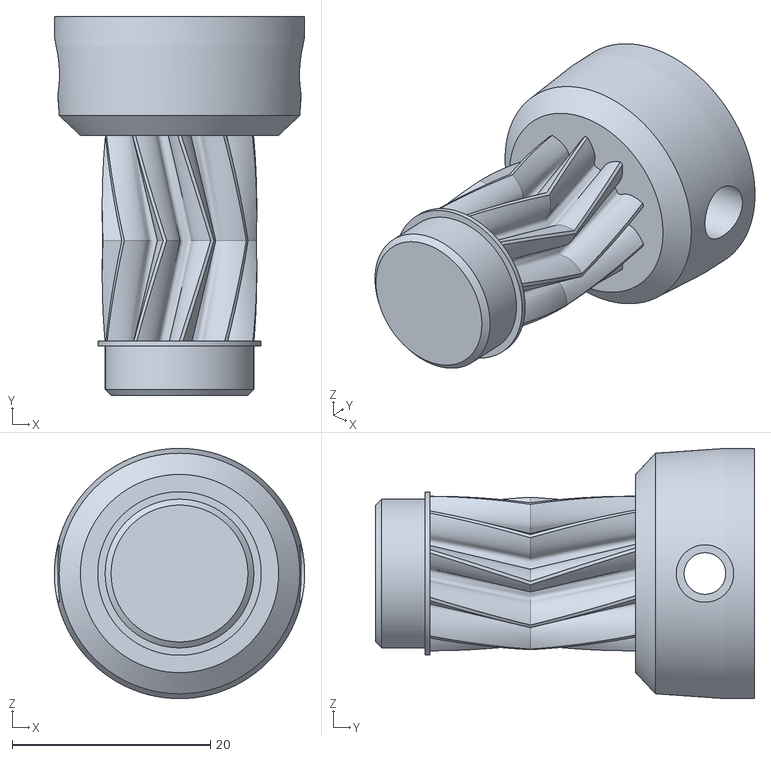
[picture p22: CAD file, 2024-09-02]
Hardwear_Car/STL/MainPart/PINION GEAR herringbone.stl
25.3 x 38.2 x 25.3

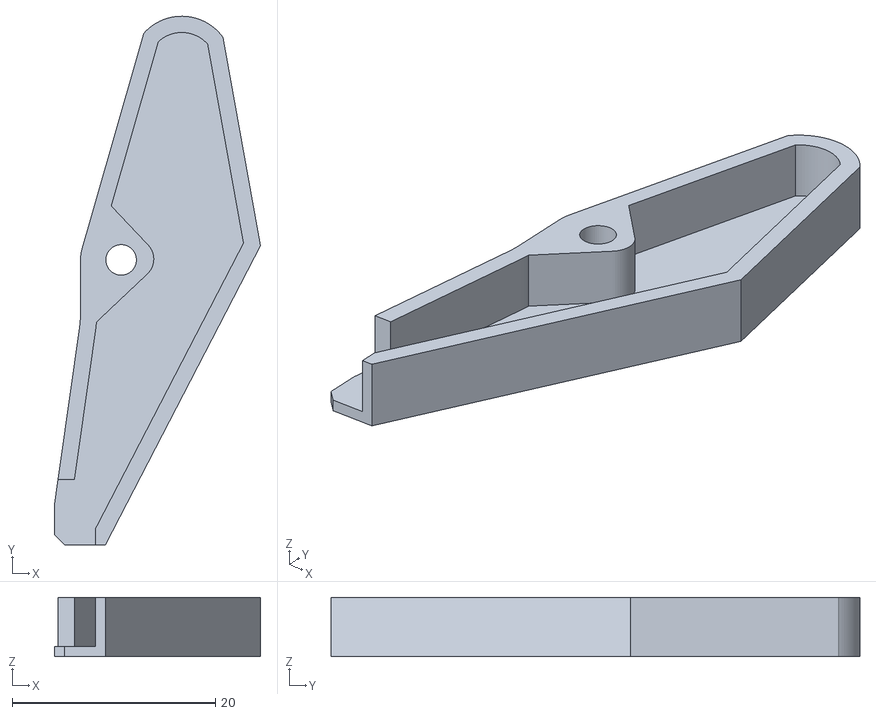
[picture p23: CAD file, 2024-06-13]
Hardwear_Car/STL/Extension/Light_Wire_Cover_H.stl
20.2 x 52.0 x 5.80

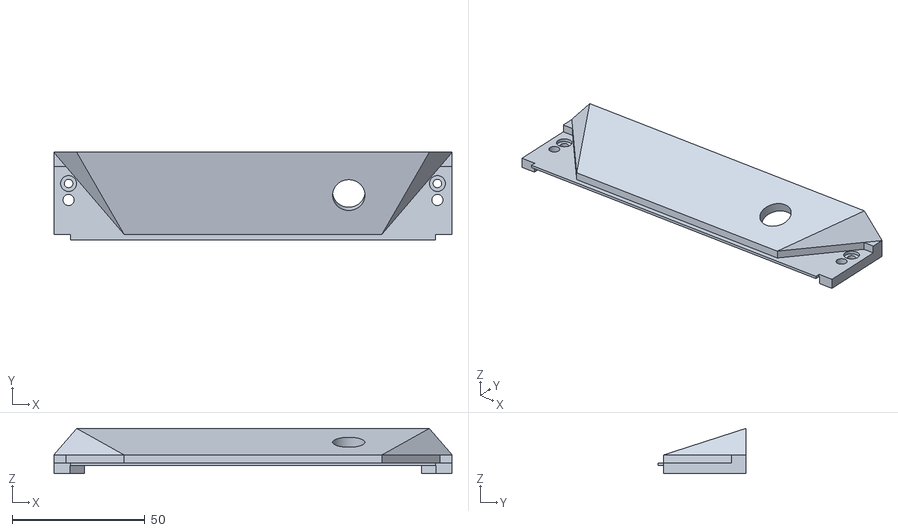
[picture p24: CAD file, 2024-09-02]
Hardwear_Car/STL/MainPart/CHASSIS Cover rear.stl
150.0 x 33.0 x 17.0

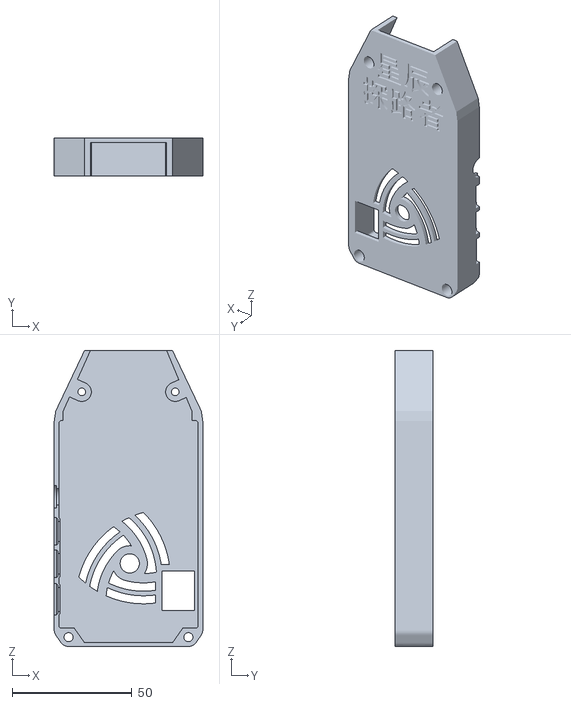
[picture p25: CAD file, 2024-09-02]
Hardwear_Car/STL/SelfDrive/FSD_Shell_cover_cn.stl
62.0 x 16.0 x 123.5

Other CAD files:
Hardwear_Car/STL/MainPart/CHASSIS_Cover.stl
Hardwear_Car/STL/Extension/Cover_rear_Light_LH.stl
Hardwear_Car/STL/MainPart/TORQUE DAMPER Fit.stl
Hardwear_Car/STL/SelfDrive/FSD_Shell_cover.stl
Hardwear_Car/STL/Extension/CrazyPowerBoard_Base.stl
Hardwear_Car/STL/Extension/SHOCK MOUNT FRONT LIGHT.stl
Hardwear_Car/STL/MainPart/Bumper.stl
Hardwear_Car/STL/MainPart/CHASSIS Cover body.stl
Hardwear_Car/STL/MainPart/CHASSIS Cover window.stl
Hardwear_Car/STL/MainPart/CONTROL ARM FIT.stl
Hardwear_Car/STL/MainPart/CV CAGE Fit.stl
Hardwear_Car/STL/MainPart/CV GEAR HOUSING Fit.stl
Hardwear_Car/STL/MainPart/CV INNER RACE.stl
Hardwear_Car/STL/MainPart/CV WHEEL HOUSING Fit.stl
Hardwear_Car/STL/MainPart/END CHASSIS B04 Fit.stl
Hardwear_Car/STL/MainPart/END CHASSIS B05.stl
Hardwear_Car/STL/MainPart/END CHASSIS B06.stl
Hardwear_Car/STL/MainPart/FRONT A PLATE Fit.stl
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

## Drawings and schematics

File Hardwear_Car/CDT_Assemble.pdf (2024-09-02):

# CrazyDonkeyTarmo Assemble Guide

V1.1

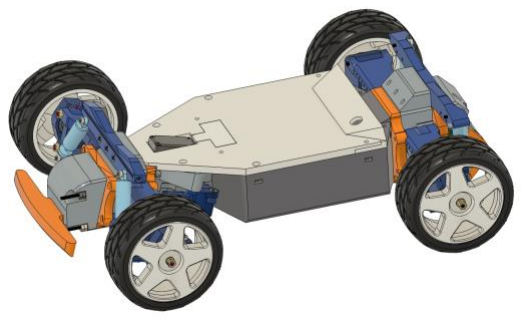
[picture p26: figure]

Table of Contents

## I. Fasten List

Name | CN | Part
M4 x 40 | M4 内六角
M4 x 35
M4 x 20
M4 x 16
M4 x 12
m3 x 20
m3 x 16
M3 x 8
M4 x 30 hex head bolts | M4 外六角螺杆
M3 Nut | M3 螺母
M3 Nylon Nut | M3 紧锁螺母
M4 Nut | M4 螺母
M4 Nylon Nut | M4 紧锁螺母
M3 Shim | M3 垫片
M4 Shim | M4 垫片
M3 Threaded Rod | 螺杆 | 350mm
Bearing | 轴承 | 6802RS
steel balls | 滚珠 | 6mm
Main Drive Gear Adaptor | 限位环 | ID: 5mm OD: 10mm H: 6mm

M4 | M3

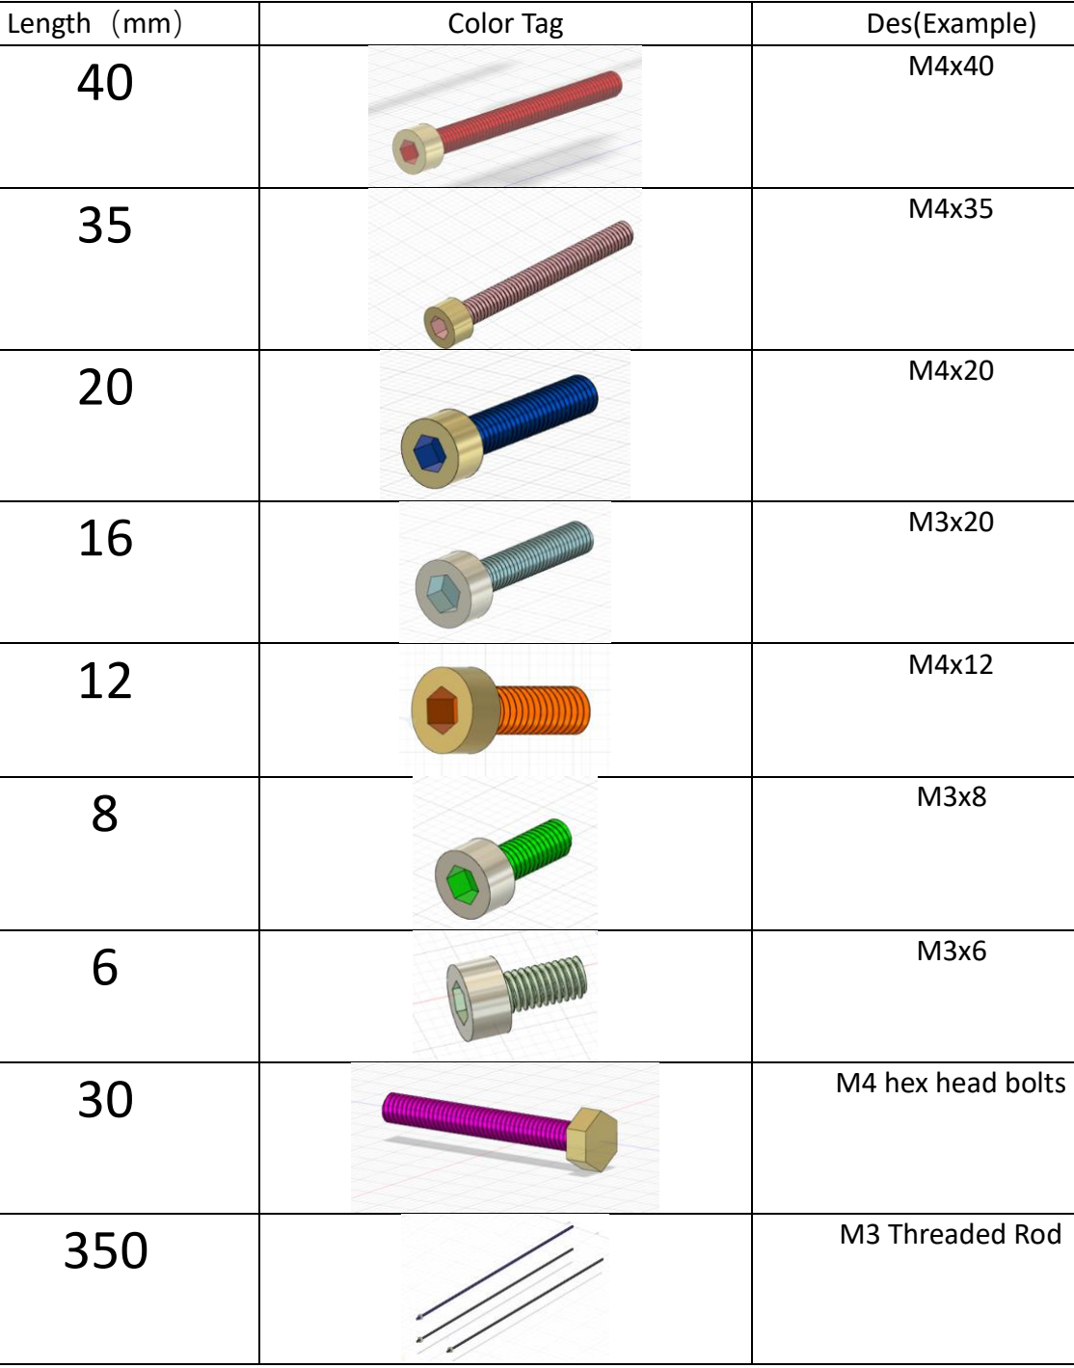
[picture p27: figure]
Length（mm）; Color Tag; Des(Example); M4 hex head bolts; M3 Threaded Rod

## II. Part 1: Rear Wheel Component

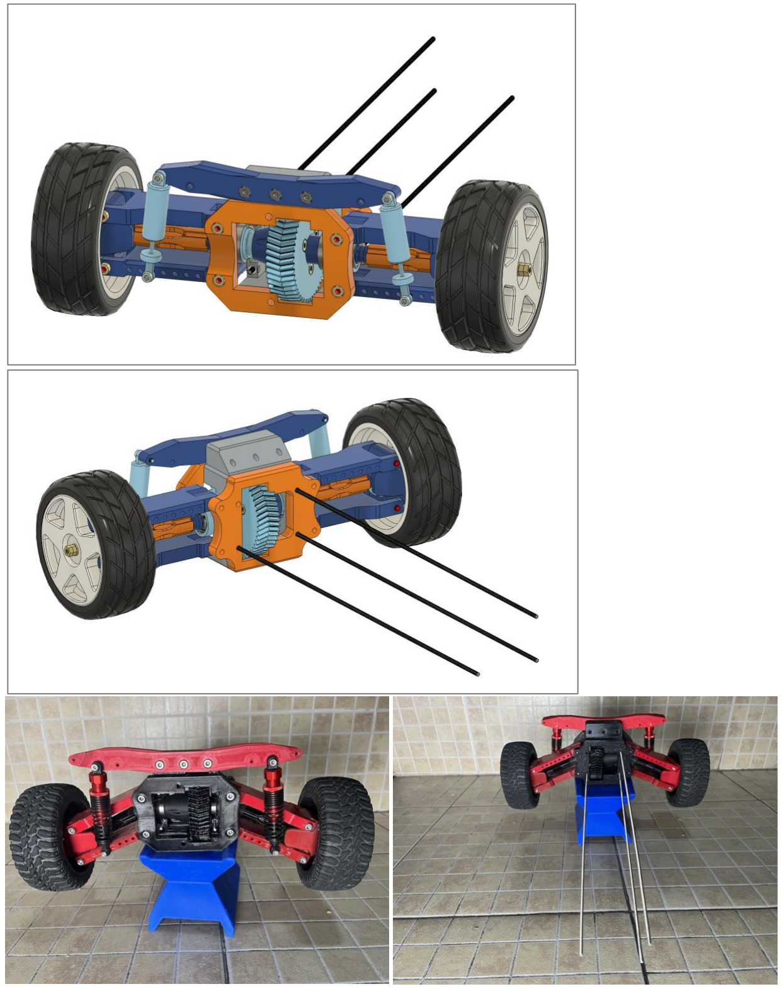
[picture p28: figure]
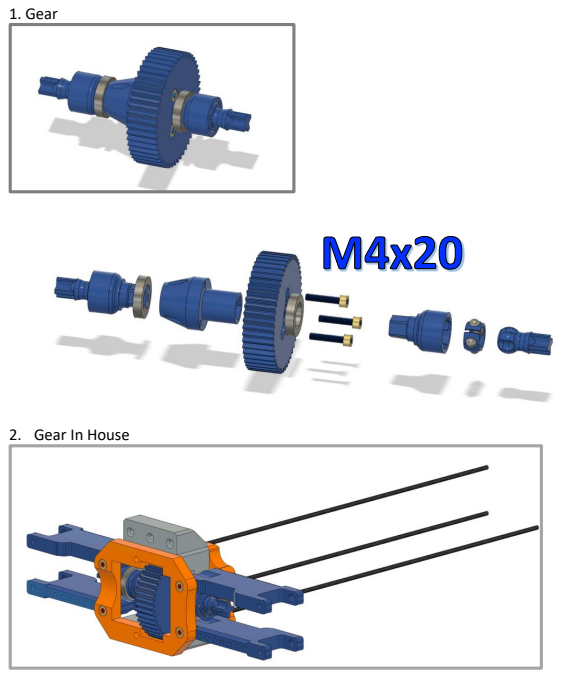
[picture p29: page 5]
1. Gear

2. Gear In House

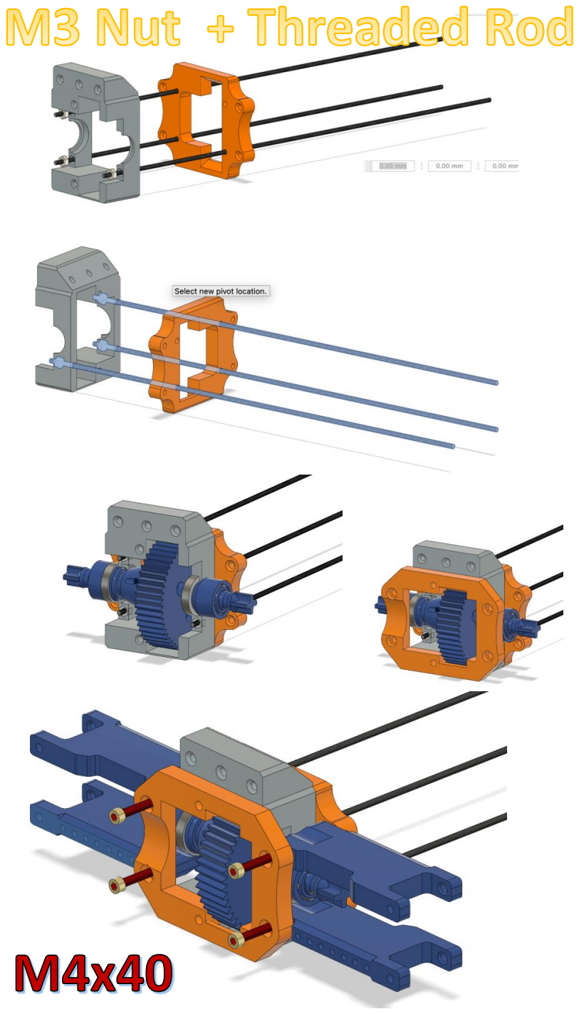
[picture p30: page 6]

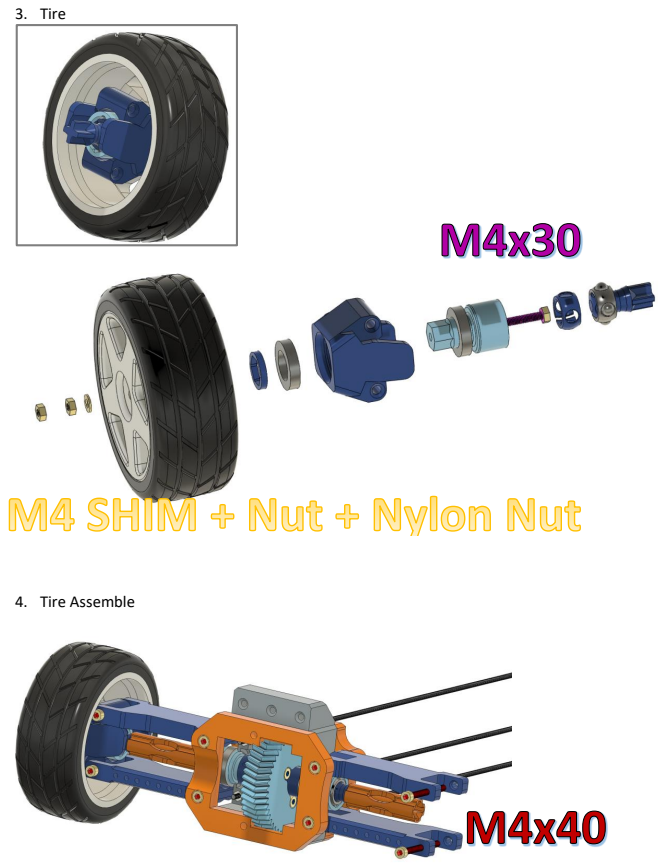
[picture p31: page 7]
3. Tire; 4. Tire Assemble

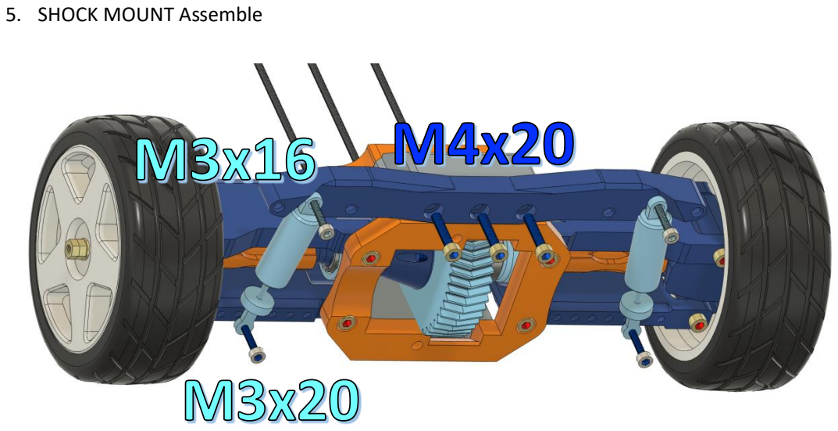
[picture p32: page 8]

5. SHOCK MOUNT Assemble

## III. Part 2: Motor Component

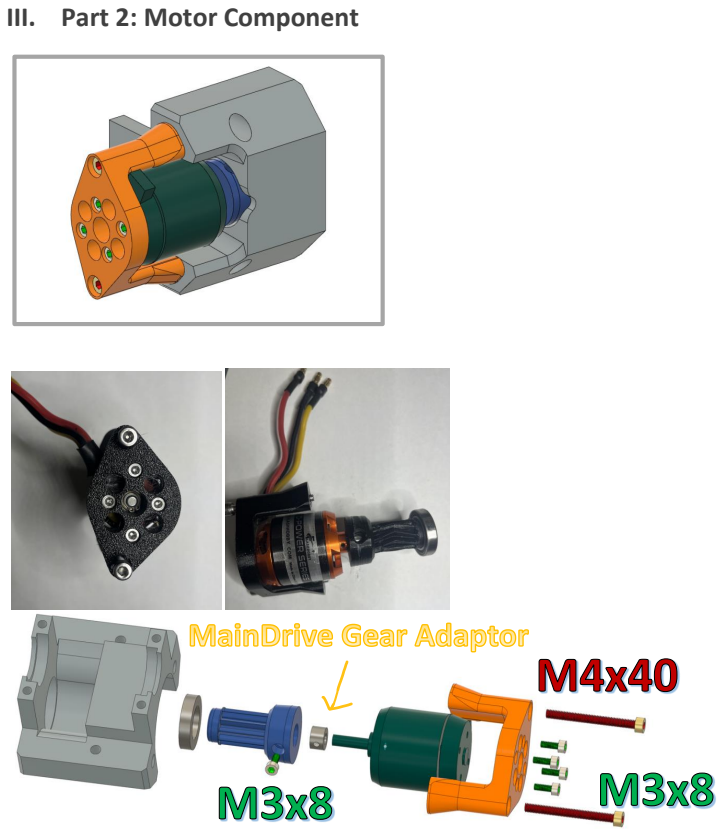
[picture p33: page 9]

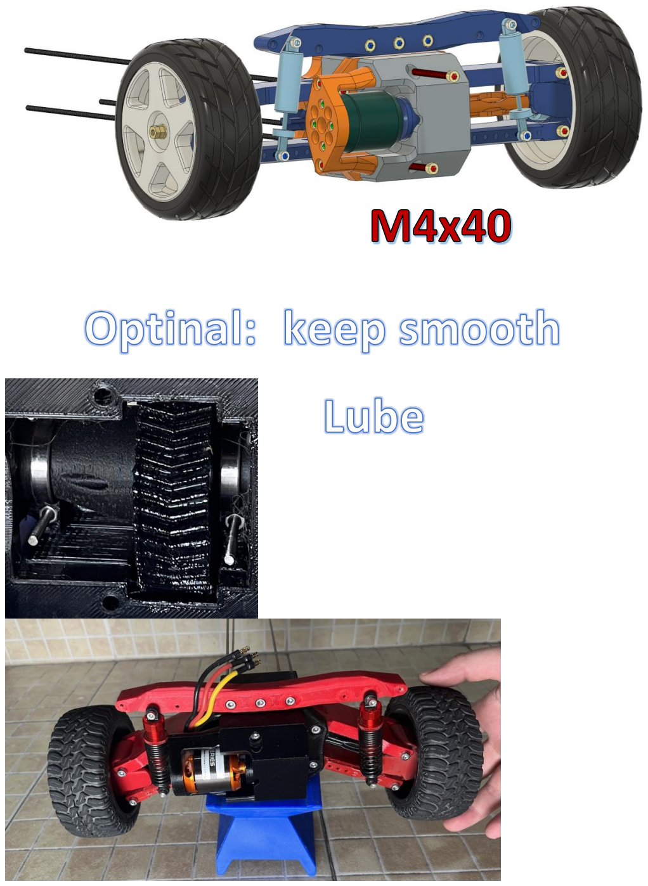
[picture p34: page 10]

## IV. Part 3: Servo Component

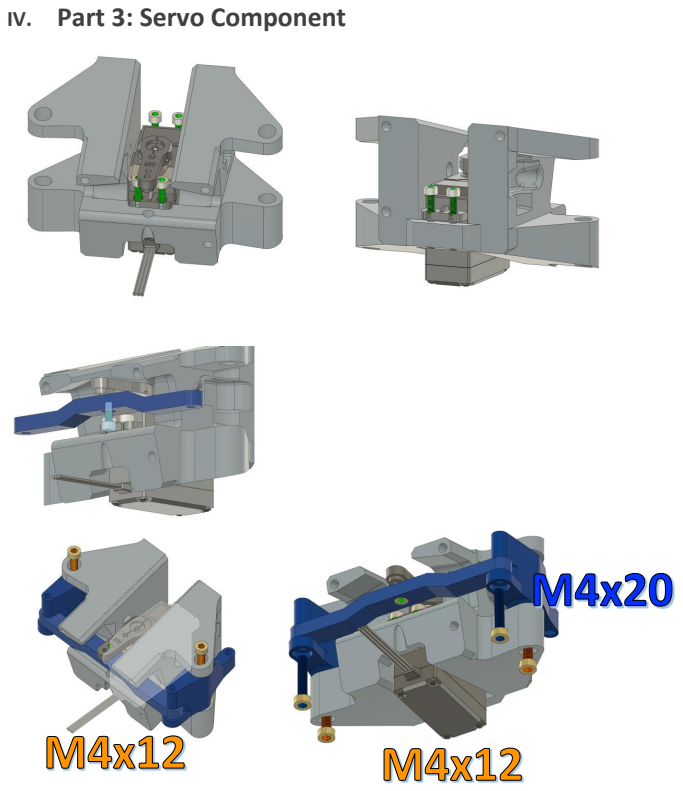
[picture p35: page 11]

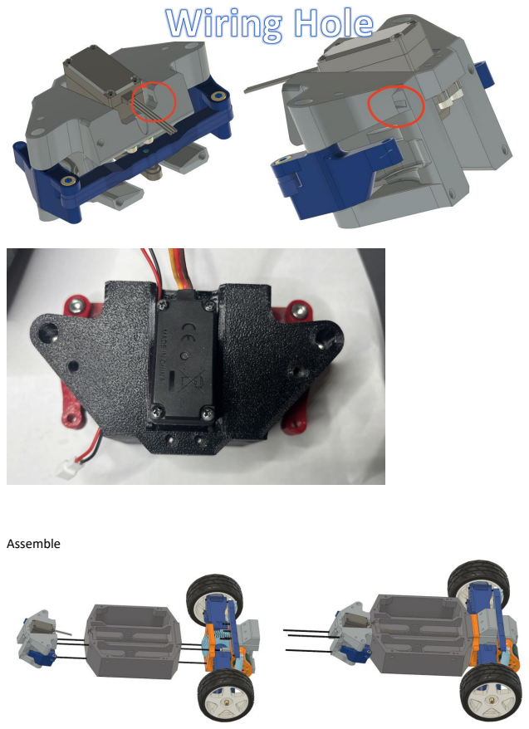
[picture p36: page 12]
Assemble

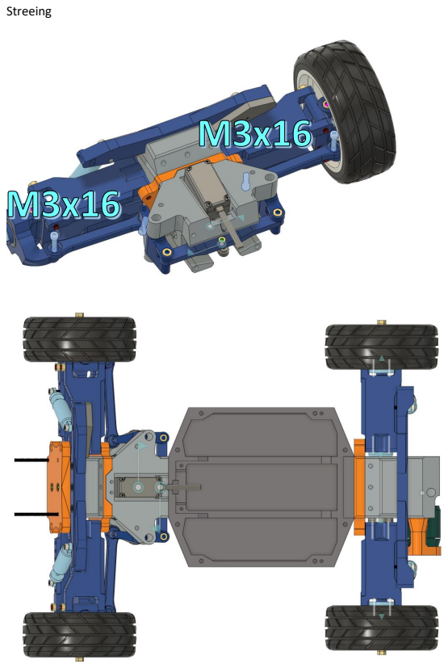
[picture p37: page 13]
Streeing

## V. Part 4: Front Wheel Component

1. Front Wheel; 2. Wheel Assemble

M3x20

Assemble

3. SHOCK MOUNT Assemble

## VI. Part 5: GUARD Component


## VII. Part 6: Plugins Component


## VIII. Part 7: Self Drive Mount


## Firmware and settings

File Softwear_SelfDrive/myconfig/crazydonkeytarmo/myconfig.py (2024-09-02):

# """ 
# My CAR CONFIG 

# This file is read by your car application's manage.py script to change the car
# performance

# If desired, all config overrides can be specified here. 
# The update operation will not touch this file.
# """

# import os
# 
# #PATHS
# CAR_PATH = PACKAGE_PATH = os.path.dirname(os.path.realpath(__file__))
# DATA_PATH = os.path.join(CAR_PATH, 'data')
# MODELS_PATH = os.path.join(CAR_PATH, 'models')
# 
# #VEHICLE
# DRIVE_LOOP_HZ = 20      # the vehicle loop will pause if faster than this speed.
# MAX_LOOPS = None        # the vehicle loop can abort after this many iterations, when given a positive integer.
# 
# #CAMERA
CAMERA_TYPE = "PICAM"   # (PICAM|WEBCAM|CVCAM|CSIC|V4L|D435|MOCK|IMAGE_LIST)
IMAGE_W = 160
IMAGE_H = 120
# IMAGE_DEPTH = 3         # default RGB=3, make 1 for mono
# CAMERA_FRAMERATE = DRIVE_LOOP_HZ
# CAMERA_VFLIP = False
# CAMERA_HFLIP = False
# CAMERA_INDEX = 0  # used for 'WEBCAM' and 'CVCAM' when there is more than one camera connected 
# # For CSIC camera - If the camera is mounted in a rotated position, changing the below parameter will correct the output frame orientation
# CSIC_CAM_GSTREAMER_FLIP_PARM = 0 # (0 => none , 4 => Flip horizontally, 6 => Flip vertically)
# BGR2RGB = False  # true to convert from BRG format to RGB format; requires opencv
# SHOW_PILOT_IMAGE = False  # show the image used to do the inference when in autopilot mode
# 
# # For IMAGE_LIST camera
# # PATH_MASK = "~/mycar/data/tub_1_20-03-12/*.jpg"
# 
# #9865, over rides only if needed, ie. TX2..
# PCA9685_I2C_ADDR = 0x40     #I2C address, use i2cdetect to validate this number
# PCA9685_I2C_BUSNUM = None   #None will auto detect, which is fine on the pi. But other platforms should specify the bus num.
# 
# #SSD1306_128_32
# USE_SSD1306_128_32 = False    # Enable the SSD_1306 OLED Display
# SSD1306_128_32_I2C_ROTATION = 0 # 0 = text is right-side up, 1 = rotated 90 degrees clockwise, 2 = 180 degrees (flipped), 3 = 270 degrees
# SSD1306_RESOLUTION = 1 # 1 = 128x32; 2 = 128x64
# 
# #
# # DRIVE_TRAIN_TYPE
# # These options specify which chasis and motor setup you are using.
# # See Actuators documentation https://docs.donkeycar.com/parts/actuators/
# # for a detailed explanation of each drive train type and it's configuration.
# # Choose one of the following and then update the related configuration section:
# #
# # "PWM_STEERING_THROTTLE" uses two PWM output pins to control a steering servo and an ESC, as in a standard RC car.
# # "MM1" Robo HAT MM1 board
# # "SERVO_HBRIDGE_2PIN" Servo for steering and HBridge motor driver in 2pin mode for motor
# # "SERVO_HBRIDGE_3PIN" Servo for steering and HBridge motor driver in 3pin mode for motor
# # "DC_STEER_THROTTLE" uses HBridge pwm to control one steering dc motor, and one drive wheel motor
# # "DC_TWO_WHEEL" uses HBridge in 2-pin mode to control two drive motors, one on the left, and one on the right.
# # "DC_TWO_WHEEL_L298N" using HBridge in 3-pin mode to control two drive motors, one of the left and one on the right.
# # "MOCK" no drive train.  This can be used to test other features in a test rig.
# # "VESC" VESC Motor controller to set servo angle and duty cycle
# # (deprecated) "SERVO_HBRIDGE_PWM" use ServoBlaster to output pwm control from the PiZero directly to control steering,
# #                                  and HBridge for a drive motor.
# # (deprecated) "PIGPIO_PWM" uses Raspberrys internal PWM
# # (deprecated) "I2C_SERVO" uses PCA9685 servo controller to control a steering servo and an ESC, as in a standard RC car
# #
DRIVE_TRAIN_TYPE = "PWM_STEERING_THROTTLE"
# 
# #
# # PWM_STEERING_THROTTLE
# #
# # Drive train for RC car with a steering servo and ESC.
# # Uses a PwmPin for steering (servo) and a second PwmPin for throttle (ESC)
# # Base PWM Frequence is presumed to be 60hz; use PWM_xxxx_SCALE to adjust pulse with for non-standard PWM frequencies
# #
PWM_STEERING_THROTTLE = {
    "PWM_STEERING_PIN": "PIGPIO.BCM.2",   # PWM output pin for steering servo
    "PWM_STEERING_SCALE": 1.03,             # used to compensate for PWM frequency differents from 60hz; NOT for adjusting steering range
    "PWM_STEERING_INVERTED": False,         # True if hardware requires an inverted PWM pulse
    "PWM_THROTTLE_PIN": "PIGPIO.BCM.14",   # PWM output pin for ESC
    "PWM_THROTTLE_SCALE": 1.0,              # used to compensate for PWM frequence differences from 60hz; NOT for increasing/limiting speed
    "PWM_THROTTLE_INVERTED": False,         # True if hardware requires an inverted PWM pulse
    "STEERING_LEFT_PWM": 200,               #pwm value for full left steering
    "STEERING_RIGHT_PWM":400,              #pwm value for full right steering
    "THROTTLE_FORWARD_PWM": 400,            #pwm value for max forward throttle
    "THROTTLE_STOPPED_PWM": 300,            #pwm value for no movement
    "THROTTLE_REVERSE_PWM": 200,            #pwm value for max reverse throttle
}
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

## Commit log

2024-06-13 feat: STL
    [Bumper.stl, CHASSIS Cover body.stl, CHASSIS Cover rear.stl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]
2024-06-13 feat: assemble guider
2024-06-24 feat: update readme, filament
2024-09-02 feat: CrazyDonekyTarmo with selfdrive
    [BOM.csv, Bumper.stl, CHASSIS Cover body.stl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]
